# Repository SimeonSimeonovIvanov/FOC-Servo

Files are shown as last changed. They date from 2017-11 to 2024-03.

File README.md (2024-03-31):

# FOC-Servo

[FOC Servo (youtube.com)](https://www.youtube.com/playlist?list=PLE616v1yP137koahQjisksADdZlHxYS2S)<br>
[Images (photos.google.com)](https://goo.gl/photos/JQcb6tujQgFE7cGe8)<br>

![Screen Shot](https://lh3.googleusercontent.com/vWZbaQVdAhu1QQO_cTlWY4MgnAb2BmGCg2ht9W3ZADUsB-J3ieZKUOjoW8N4zHFRGdZp8hFGPKCy6uawGKFupMPxBJmIFaj5hGluz3LkEmy5S17hmuiLZEQlVxxbsq9VOWg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)<br>
![Screen Shot](https://lh3.googleusercontent.com/k02gDKrigeXRs4gnt29zIekYWgJM7NDDvpPBwwBkn84v4wwCzqt8nw-INf11CDgn7xQ7Py5mxIiK_7V0SbNQoPlOT3bTszP4-zwKSuMI01aGK7_4IhnsZZ5Z7r1dPS8m6I9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)<br>

http://mcu-bg.com/mcu_site/viewtopic.php?p=226271#p226271:<br>
"След аналоговото DC-Servo (viewtopic.php?f=22&t=13129) започнах работа по BLDC-Servo. Работих по хардуерен синусоидален контрол на AC Servo motor (PMSM) с три токови ШИМ-а. Успях да постигна токова регулация в 6 стъпкова комутация. Синусоидален режим така и не подкарах напълно. Но в крайна сметка това беше само за упражнение. Целта през цялото време беше векторно управление (FOC) на мотора. Самия мотор претърпя малка реконструкция - изведох сигналите за комутация UVW навън през RS422 предавател.

В крайна сметка стигнах до FOC-Servo. За момента имам реализирано векторно управление на базата на STM32F4. Липсва обратна връзка по скорост. Директно задавам позиция от импулсен генератор. Работи добре, има още какво да се желае.

Редно е да отбележа, че токовата обратна връзка минава през модули от честотни задвижвания на Electroinvent. Също и импулсното захранване на електрониката е от компоненти / схема (свалена от платка) на тяхно задвижване. Първоначално силовия мост беше с импулсни DC/DC преобразуватели но в случай на пробив на транзистор си 'заминаваха' набързо. Също SVPWM е копиран от кодa на STM FOC SDK v1. Другите компоненти (софтуер/хардуер) са смесица от мои и чужди проекти.

Продължавам работа по задвижването, изкушавам се да бъде част от бъдещо обновяване на ROBKO-01."

http://mcu-bg.com/mcu_site/viewtopic.php?p=235621#p235621:<br>
"Вече задвижването се захранвана директно от мрежата ( 220 VAC -> 320 VDC на моста ). Изпитвах доста притеснения в етапа на увеличаване на напрежението. Разбира се имаше и проблеми. Сред които особено неприятна осцилация на GS на полевите транзистори. Успях да затворя и позиционния и скоростния контур. За жалост обратната връзка по скорост все още е прекалено груба и това създава проблеми но все пак работи доста добре.

Файловете на проекта са качени в https://github.com/SimeonSimeonovIvanov/FOC-Servo
Видео от отделните тестове: youtube.com / FOC Servo"

http://mcu-bg.com/mcu_site/viewtopic.php?p=277382#p277382:<br>
"Да се похваля :) От проекта за FOC Servo (open source) успях да достигна до нещо много по-истинско: AC Servo. Засега не съм решил дали ще премине към open или close. Отделни схемни решения от него са качени в git: https://github.com/SimeonSimeonovIvanov/"

# AC-Servo
[AC Servo ( MCU v.0.0.1 / IPM v.0.0.2 ) (photos.google.com)](https://photos.app.goo.gl/KCEzDaz5cRpWHHwj6)<br>
[AC Servo (photos.google.com)](https://photos.app.goo.gl/785x7djrvYAcP9JZ6)<br>
[AC Servo ( Work ) (photos.google.com)](https://photos.app.goo.gl/srzg5DDZzGg4B8dc7)<br>

![Screen Shot](https://lh3.googleusercontent.com/InO0-X00L5HjlXPxuh1YEjHJFSkUZFtOApBEi4UaxSTPb9P_QFyURlaM9I8N8cGii7pULpo6o4EXxeGouaYiY4lC6Kz6RivBfqiPAh9K2oRpcYkvYIHu17OkECJ6e2FBvHD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)<br>

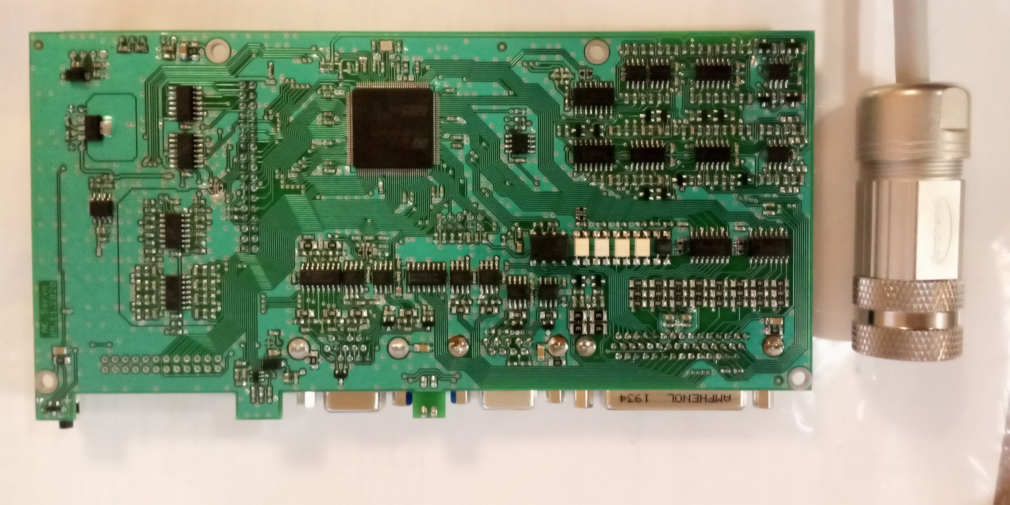
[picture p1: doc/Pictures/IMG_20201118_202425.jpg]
<br>
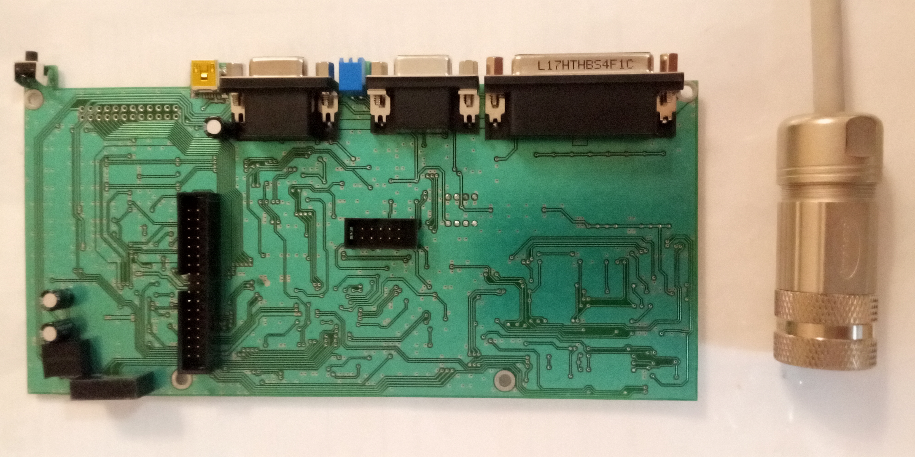
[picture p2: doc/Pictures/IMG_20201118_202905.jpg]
<br>

MIGE 80ST-M02430<br>
https://youtu.be/u-dZzM7kjZM: 300 to 3000 rpm<br><br>
SANYO DENKI P50B04006DXS40E<br>
https://youtu.be/c_Dg6a0bA2k: IN: 230 VAC; DC Bus: 325 VDC<br>
https://youtu.be/9ND_6Mmglnc<br>
![Screen Shot](https://lh3.googleusercontent.com/okfIJzOqILg2Vj1FPi2K5oUJk9owYkxtr5FeaoL3CWSu0oE8lGGliDmks5RnoqhALW29WYXMFR0nzFvj4oWKjR9dDEuZ9FIdgU9OOmerqA_8B_PouIPbHv3mtwUzUjZpZbU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)<br>

AM3024-0C21-0000<br>
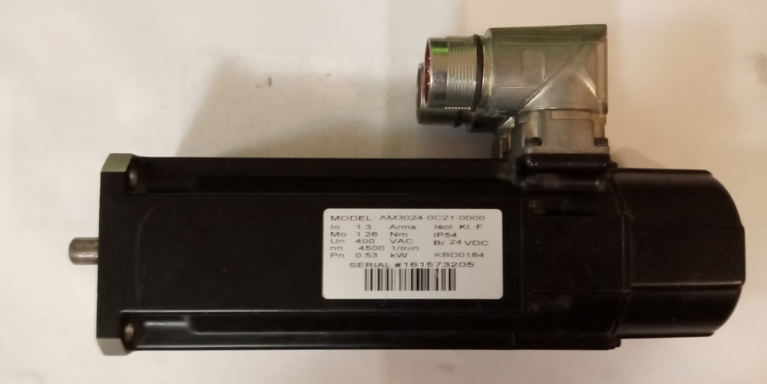
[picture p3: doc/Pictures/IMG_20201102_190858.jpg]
<br>

XML-SE30AЕКЕ<br>
https://youtu.be/lwz9wlfNBrg?si=XCSkZ5ty04_A1IbP<br>
https://youtube.com/shorts/MPl2bm2EVfs: AC Servo and Grlb - before bearing replace<br>
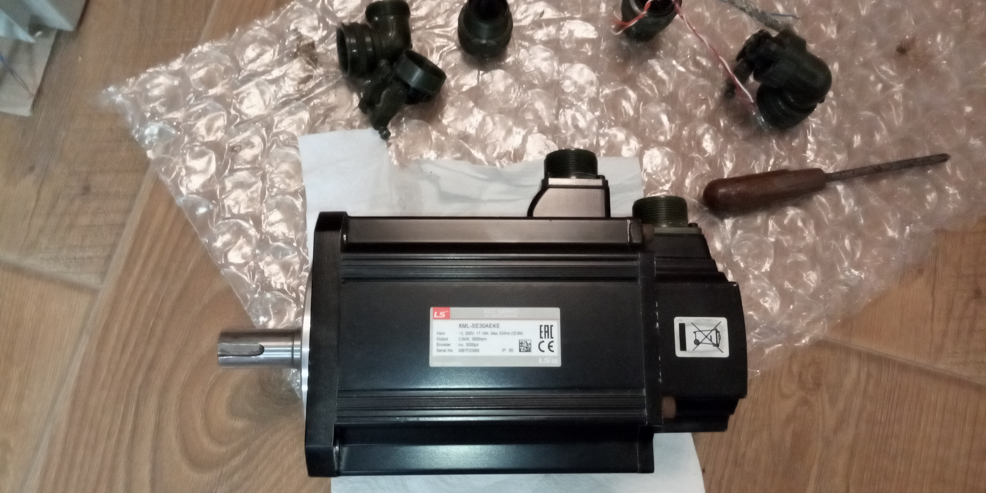
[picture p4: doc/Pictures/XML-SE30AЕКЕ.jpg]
<br>

APM-SC08ADK-52<br>
https://youtu.be/YavCcIHJMfQ?si=W7gMHxK1SwErK5KL<br>

# Simulation:

FOC.grf.png:
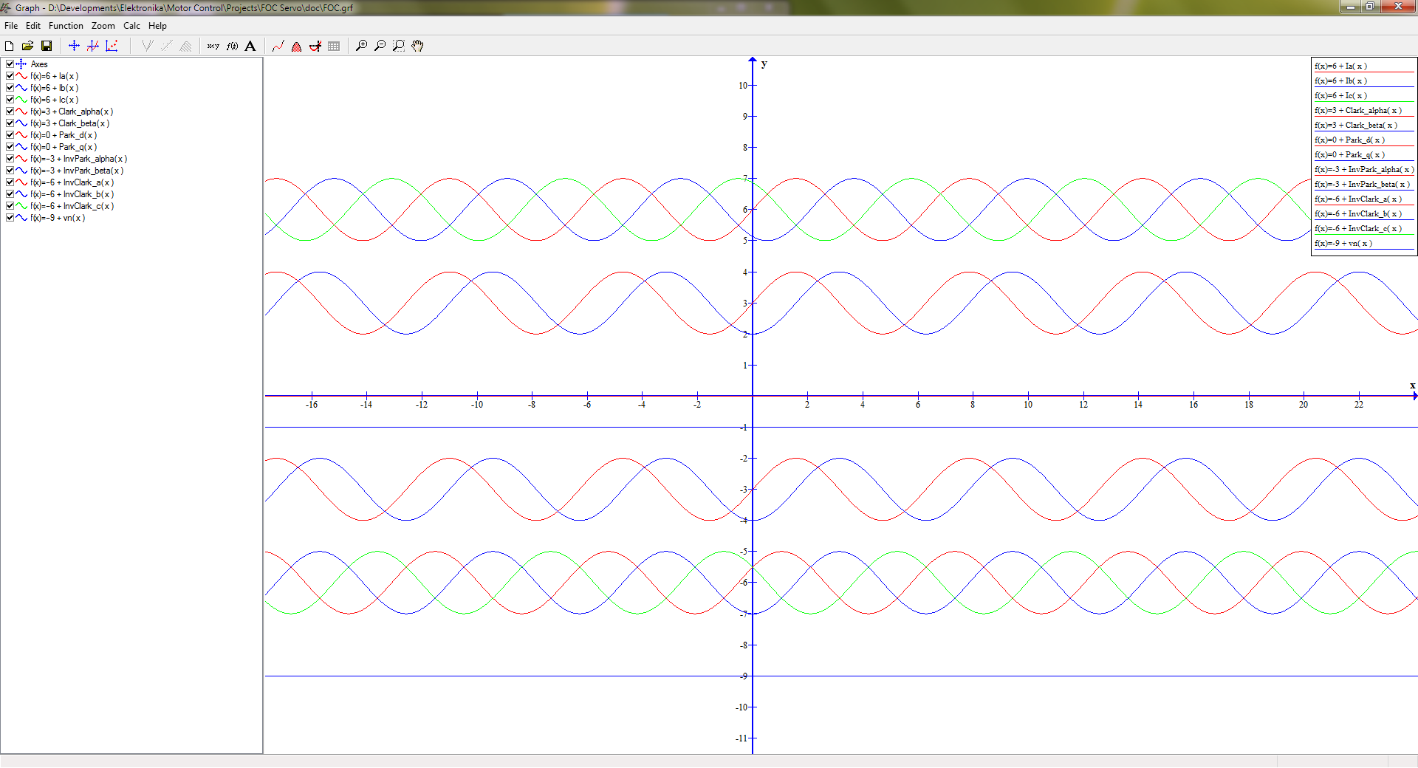
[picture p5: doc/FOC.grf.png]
<br>

ATAN.grf.png
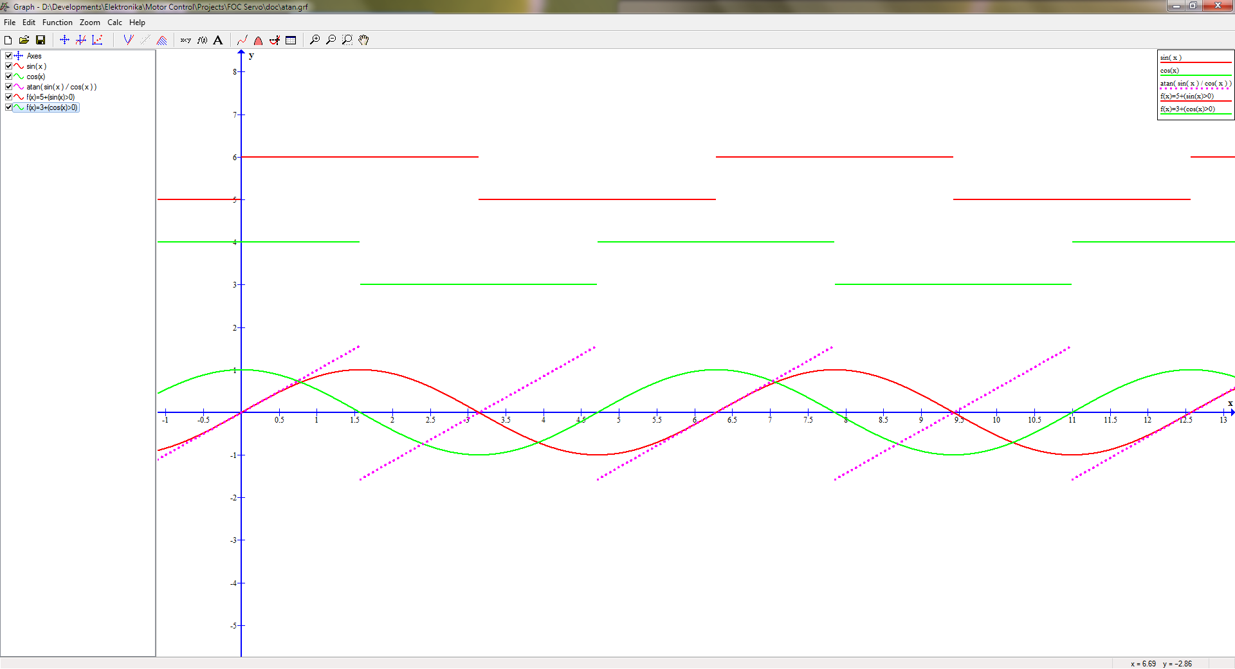
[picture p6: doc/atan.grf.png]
<br>

Sin/Cos Encoder:
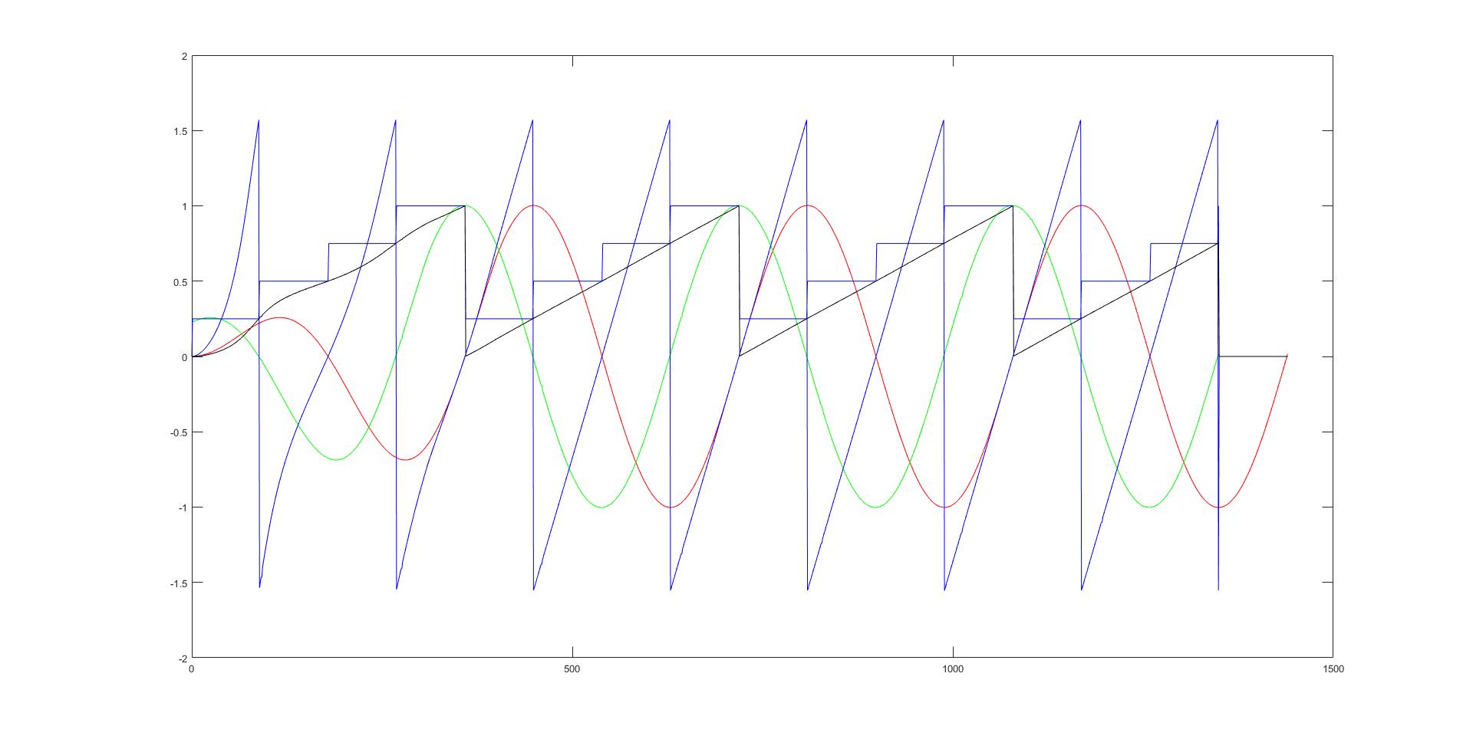
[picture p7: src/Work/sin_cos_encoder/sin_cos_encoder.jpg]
<br>

Bipolar Analog Output:
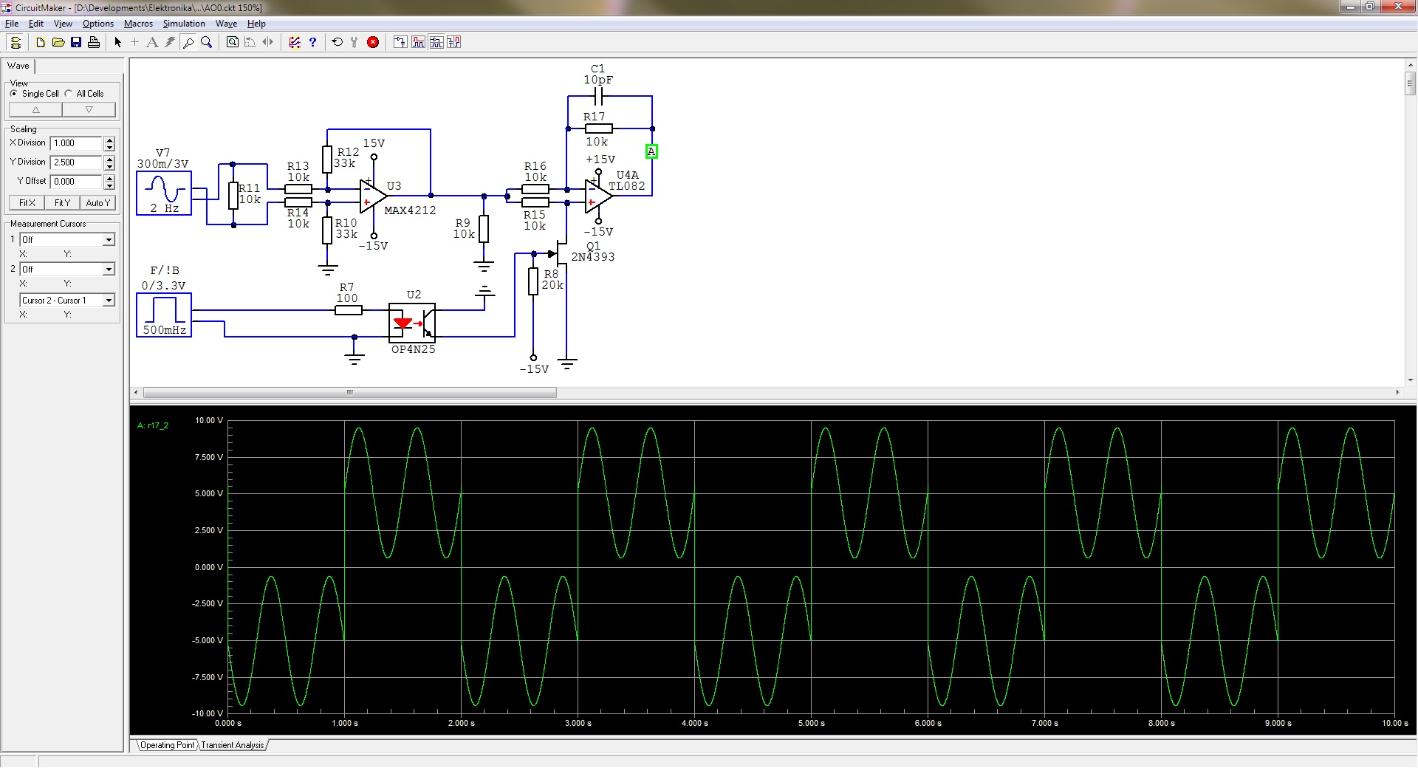
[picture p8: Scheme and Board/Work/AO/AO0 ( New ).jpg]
<br>

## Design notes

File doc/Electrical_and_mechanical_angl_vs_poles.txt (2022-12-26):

https://www.researchgate.net/post/Is_there_a_relation_between_the_electrical_and_mechanical_angle
========================================================================================================================
Nebi Caka
University of Prishtina
In a multipolar electrical machine (motor or generator), relationship between the mechanical angle and electrical angle is given by:
Electrical angle = (P/2) x Mechanical angle
where: P = Number of poles
So:
- In a two-pole motor (P = 2): Electrical Angle = Mechanical Angle
- In a four-pole motor (P = 4): Electrical Angle = 2 times Mechanical Angle
- In a six-pole motor (P = 6): Electrical Angle = 3 times Mechanical Angle
etc.
========================================================================================================================
Aderiano da Silva
Rockwell Automation
For asynchronous machines, the electrical angle (thetaE) is related to the mechanical angle (thetaM) in terms of the number of poles (N) as follows:
thetaE = (N/2) * thetaM
========================================================================================================================

Pole pairs = Poles / 2

Electrical angle = (Poles / 2) x Mechanical angle
Electrical angle = Pole pairs x Mechanical angle

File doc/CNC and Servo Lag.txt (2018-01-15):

http://www.practicalmachinist.com/vb/cnc-machining/lag-error-234762/#post1679838

 mike_kilroy
mike_kilroy is offline Stainless 

system gain (amount of "lag" error) is SET by the analog velocity speed scale adjustment pot on the servo drive amplifier. it was typically set to 1IPM/MiL on that vintage machine. that means if u run 100IPM u will have .100" or 100 mills of following ("lag") error. 400ipm means .4" so u can see the faster u go the more lag.

then there is a max lag error shut off point - maybe 1" or so in the above ex for a machine that can run to 400ipm.

yes, if it used to work somethng likely changed so mechanics is first thing to look at; if friction increases then the lag might increase (depends on the servo drive design - if it has integral gain - the I in PID loop then it takes a LOT of extra friction to bother this).

if you can turn the screw by hand easy and dont think it changed it could be aging of electronics and a simple readjust of speed pot on Y axis servo drive will bring it back.

remember that WHEN something brakes it is usually the last thing we did that caused it to brake.... so think back..... did this y shake and error start suddendly? after a crash? or did it creep up on you getting worse and worse -- over 1 day? 1 hour? 2 years? these r all good clues to help point to the culprit

if u can see lag error and speed on ur nc screen, check all axis; they shyud be the same. if u see y has bigger lag at a given speed, adjust the speed pot on the drive to make it the sanme as the other axes. if u dont know where the speed pot is, tell us the drive mfgr and model cuz some of us may know

too hi or too lo gain will cause the same y axis oscillation or jerkyness you see.

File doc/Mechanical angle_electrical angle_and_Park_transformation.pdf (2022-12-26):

Electrical Engineering Stack Exchange is a question and answer site for electronics and electrical engineering professionals, students, and enthusiasts. It only takes a minute to sign
up.

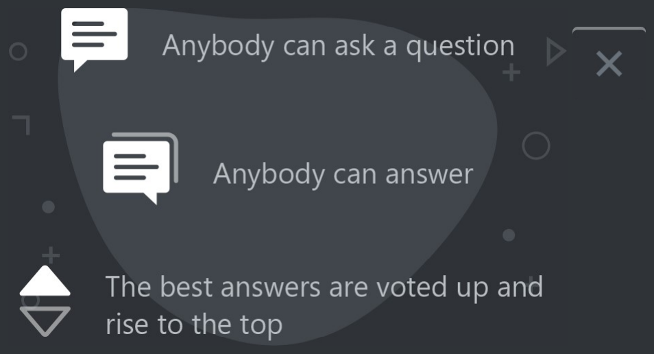
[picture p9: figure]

# Mechanical angle, electrical angle, and Park transformation

Asked 5 years, 7 months ago Modified 5 years, 2 months ago 2k times Viewed
0

I have a question about the electrical angle and mechanical angle of the BLDC motor. The motor has 8 poles. We have
Electrical angle = number of pole pair * mechanical angle
This would mean that if the mechanical angle covers 45 deg, the electrical angle has spanned 360 deg. After that, should I reset my electrical angle to 0 and start counting again, or it's acceptable if the electrical angle keeps increasing?
I use the electrical angle in the Park transformation for calculations.
microcontroller motor
Share Cite Follow | edited Oct 25, 2017 at 10:03
raggot
415 4 16

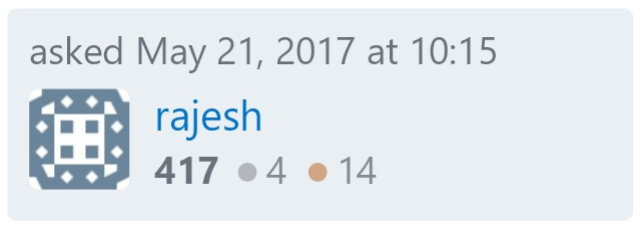
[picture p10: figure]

1 Robert Park was a man- please capitalize his name in your title and text. – Spehro Pefhany May 21, 2017 at 10:37
I am sorry. Can i edit now. – | May 21, 2017 at 10:49
1 Answer | Sorted by: Highest score (default)

1

What is key is the electrical frame of reference. Every pole-pair the cycle completes.
For a 6 pole machine, 3pole-pair, this wrap (in the mechanical frame of reference) is every 120degrees
For an 8 pole machine, 4pole-pair, this wrap (in the mechanical frame of reference) is every 90degrees.
If you unwrap a machine stator (see below for a 2pole-pair) the difference becomes clear

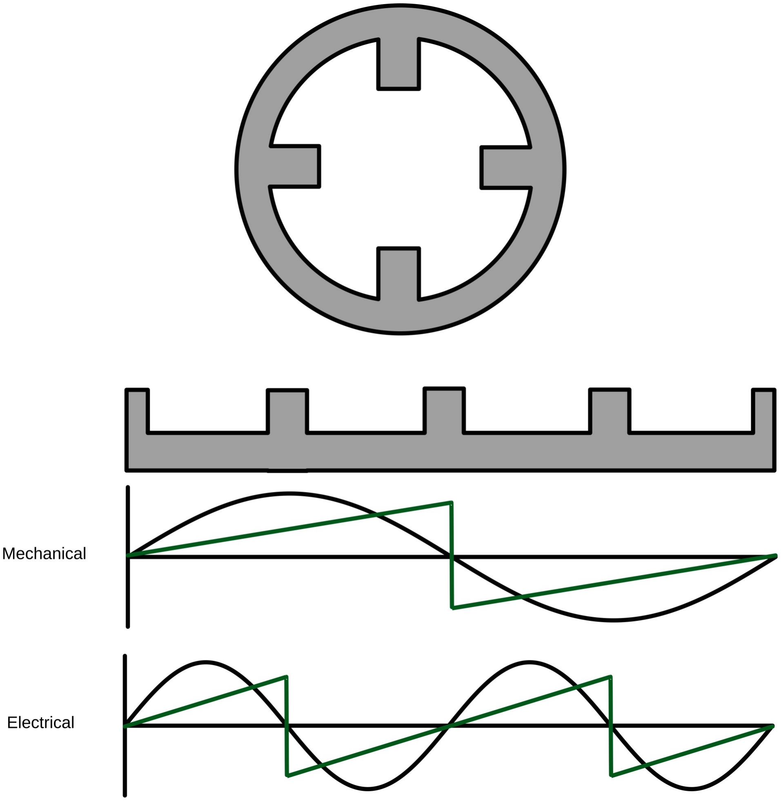
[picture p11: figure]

Share Cite Follow | answered May 21, 2017 at 10:58
user16222

No i am not able to understand. – May 21, 2017 at 11:06
What exactly don't you understand – user16222 May 21, 2017 at 11:11
If my mechanical angle is 360 then electrical angle will be 8 * 360 degrees, if it is 8 pole pair. Please help. – May 21, 2017 at 11:12
The electrical angle would be 0 or 4*360 (as 0=360) if you were to unwrap the angle. I do not know you low level implementation but the usual method is to calculate mechanical, multiply by pole-pair count & ensure the register wraps – user16222 May 21, 2017 at 11:15
void encoderInterrupt(void) { encoderincr++; mechanical_angle = encoderincr * 360 / ENCODER_COUNTER; /* ENCODER_COUNTER is the number of counts for one revolution */ if(mechanical_angle > 360) { encoderincr=0; } electricalangle = NOPOLEPAIR * mechanical_angle; } – May 21, 2017 at 11:51

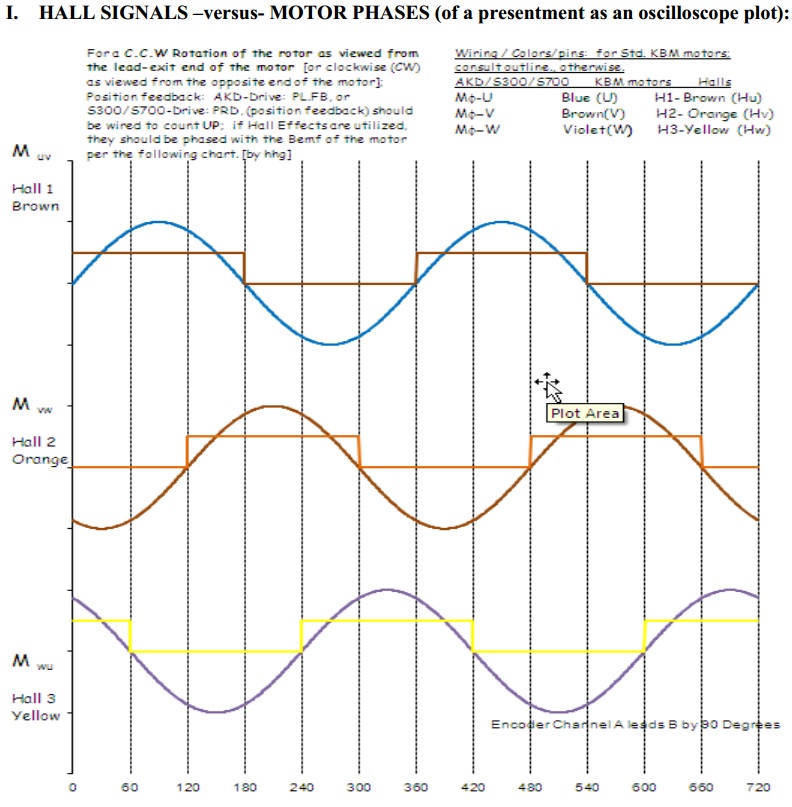
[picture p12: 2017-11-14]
doc/HALL/HALL vs PHASE.jpg

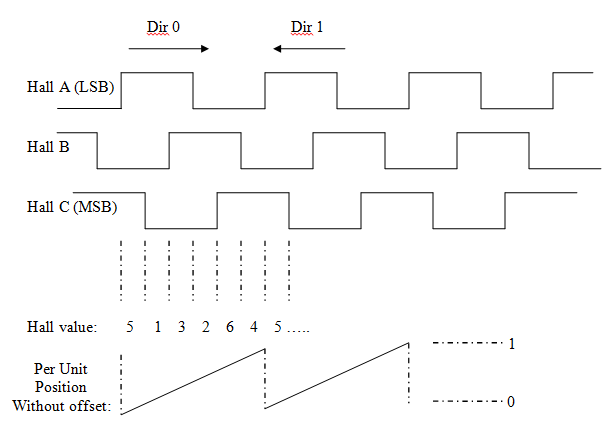
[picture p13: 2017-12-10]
doc/HALL/xxc2812pmsmfoc_Hall_signals.png

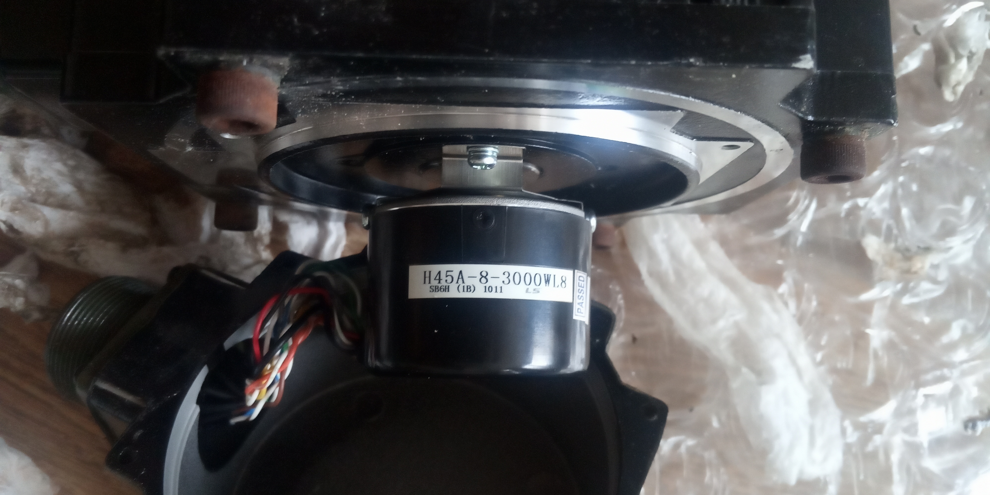
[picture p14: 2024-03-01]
doc/Pictures/H45A-8-3000WL8.jpg

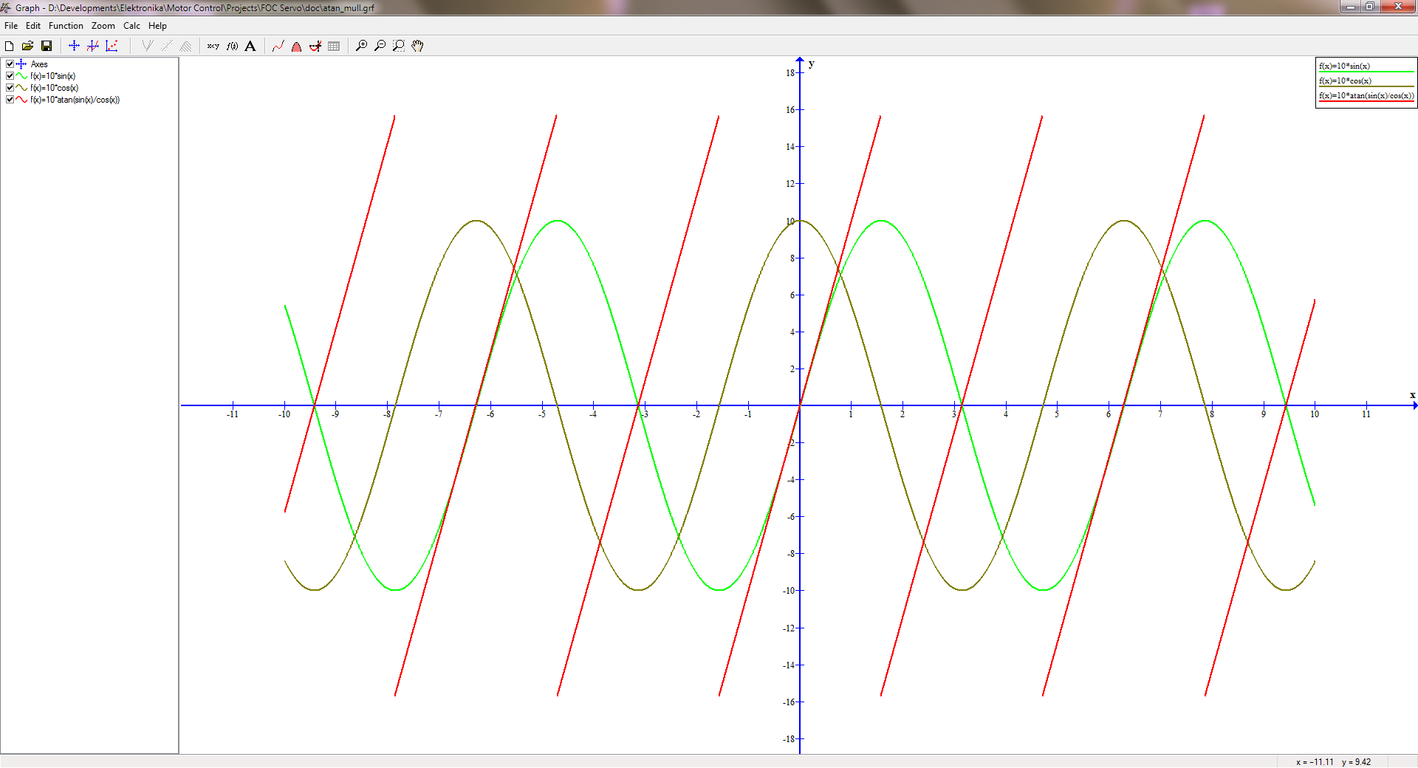
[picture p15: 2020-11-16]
doc/atan_mull.grf.png

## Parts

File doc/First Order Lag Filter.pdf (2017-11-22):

# First Order Lag Filter

The formula for a first order lag filter is fairly simple:

new_filtered_value = k * raw_sensor_value + (1 - k) * old_filtered_value

The "magic" is determining an approprate value for 'k'. The hard approach is to characterize the noise which will be present in the system and do some frequency-domain calculations to diminish the noise to acceptable levels. One thing that makes this approach hard (or even impossible) is that it requires knowing what noise sources will be present and what their frequency and magnitude characteristics will be. The easier approach is to cast a wide net and just filter the hell out of the signal.

The one catch with the easy approach is known as "lag". That is, when the input changes, the filtered value may not reflect enough of the change fast enough to meet system response requirements. For example, if you are using an IR LED and IR sensor to detect when you are within a short distance of an obstacle, too much filtering may result in the sensor not indicating there is an obstacle until after you run into the obstacle (or after there is insufficient time to stop).

The good thing about working from the perspective of lag is that determining how much lag is acceptable is generally easier than characterizing noise. Consider the previous example about running into an obstacle. If you know that you read the sensor 50 times a second, that you need the filtered value to reach 90% of the actual sensor value before your robot will think there is an obstacle, and that (based on your robot's speed and the sensor range) you need the filtered value to reach that level within 0.3 seconds, then you have all of the data you need to calculate 'k'.

The following sections will:

Explain the input data you need to provide.
Show how to calculate a suitable value for 'k' based on your input.

## Input #1: Maximum Response Time (Tr)

This is the (maximum) amount of time (in seconds) between the instant the raw sensor value changes and the instant the filtered sensor value reflects that change.

For example, say your robot has an IR sensor that detects obstacles within 1 meter and your robot requires 0.2 meters to come to a complete stop. That means your robot can continue traveling full speed at most 1 - 0.2 = 0.8 meters after the sensor detects an obstacle.

Furthermore, say your robot's full speed is 2 meters/second. That means your robot needs to start stopping at most 0.8 / 2 = 0.4 seconds after the sensor detects an obstacle.

Finally, you decide you don't want to set things up so your robot just barely manages to stop in time (with its nose right against the obstacle). Instead, you would like to leave some margin for error. So rather than using 0.4 seconds, you go with a
maximum response time (Tr) of 0.3 seconds (leaving you a 0.1 second margin of error).

## Input #2: Sampling Period (Ts)

This is the amount of time (in seconds) between one reading of the raw sensor value and the next.

For example, if the robot samples the sensor 50 times a second, then the sampling period (Ts) is 1 / 50 = 0.02 seconds. (This is assuming that the sensor is read at roughly regular intervals.)

Note: Your sampling period should generally be at least 4 times (and preferably 10 times or more) smaller than your maximum response time.

## Input #3: Desired Fraction of Change (Frac)

This is the (minimum) accuracy with which a change in the raw sensor value (at time t) will be reflected in the filtered sensor value (at or before time t + Tr).

For example, suppose the output from your IR sensor changes from 0 volts to 2 volts when an obstacle comes into range. Furthermore, your robot considers any value > 1.8 volts to indicate there is an obstacle present. That means that your robot needs to see 1.8 / 2 = 0.9 (90%) of the change before the change will be acted upon, so Frac is 0.9 in this case.

## Calculate k

To calculate k, enter Tr, Ts and Frac from above into the following equation:

k = 1 - eln(1 - Frac) * Ts / Tr

where:

"e" is approximately 2.71828182846, and
"ln" is the natural logorithm function.

For the example values given in the previous sections (Tr = 0.3, Ts = 0.02, Frac = 0.9), k comes out to be about 0.142304101409.

## Results

So, does it actually work as advertised? To demonstrate it in action, the following C code is used:

void test() {
const double Ts = 0.02;
const double k = 0.142304101409; const double old_raw_sensor_value = 0;
const double raw_sensor_value = 2;
double t = 0;
double filtered_value = old_raw_sensor_value; // assume we have settled on the old value do {
filtered_value = k * raw_sensor_value + (1 - k) * filtered_value;
t += Ts;
printf("t = %.02f: filtered value = %.8f\n", t, filtered_value); } while (t < 0.4);
}

And the output produced is:

t = 0.02: filtered value = 0.28460820 t = 0.04: filtered value = 0.52871549 t = 0.06: filtered value = 0.73808531 t = 0.08: filtered value = 0.91766095 t = 0.10: filtered value = 1.07168223 t = 0.12: filtered value = 1.20378566 t = 0.14: filtered value = 1.31709023 t = 0.16: filtered value = 1.41427109 t = 0.18: filtered value = 1.49762271 t = 0.20: filtered value = 1.56911306 t = 0.22: filtered value = 1.63043004 t = 0.24: filtered value = 1.68302136 t = 0.26: filtered value = 1.72812872 t = 0.28: filtered value = 1.76681712 t = 0.30: filtered value = 1.80000000 t = 0.32: filtered value = 1.82846082 t = 0.34: filtered value = 1.85287155 t = 0.36: filtered value = 1.87380853 t = 0.38: filtered value = 1.89176609
t = 0.40: filtered value = 1.90716822

As you can see, the desired filter value (1.8) was achieved in the desired response time (0.3 seconds).

## Beyond k

Handling Startup

What do you do at the start of time? The lag filter formula is undefined because you don't have an "old_filtered_value" yet. Some approaches for computing the very first filtered value are:

Use the raw sensor data instead of the lag filter formula.
Use some "safe" value.
Use the raw sensor data adjusted towards some "safe" value. (Adjust it enough so that the adjustment is likely to be larger than any noise.)

Another option which can be combined with the above is to simply ignore the filtered sensor data entirely until several samples have been run through the filter. (For example, ignore the sensor for 'Tr' time after startup.)

Scaled Integer Math

k is always some value between 0 and 1, and rounding to 0 or 1 is no good, so a straight-forward implementation involves the use of floating point or fixed point. If you are operating in an environment where neither floating point nor fixed point are available/desirable, and you have adequately large integers at your disposal, scaled integer math can be used instead.

Scaled integer math is basically the same as fixed point, except the location of the binary point is implicit in your code. The following is some example code that only uses integer operations (add, subtract, multiply, shift) to implement a lag filter:

// shift_amount is the number of bits past the binary point.
// k_scaled is k times 2 to the power of shift_amount, rounded to the next largest integer.
// The expression "((1 << shift_amount) - k_scaled)" can, of course, be precomputed.

scaled_filtered_value = k_scaled * raw_sensor_value + ((((1 << shift_amount) - k_scaled) * scaled_filtered_value) >> shift_amount)

filtered_value = scaled_filtered_value >> shift_amount

Note that the second product will require the largest number of integer bits. You can reduce the amount of bits required by feeding "filtered_value" instead of "scaled_filtered_value" into the equation (and then removing the ">> shift_amount" in that same equation), but that negatively impacts the accuracy and can result in the 'filtered_value' getting stuck before reaching its target value.

Last Modified: November 11th, 2006
home: http://my.execpc.com/~steidl/e-mail: steidl@execpc.com

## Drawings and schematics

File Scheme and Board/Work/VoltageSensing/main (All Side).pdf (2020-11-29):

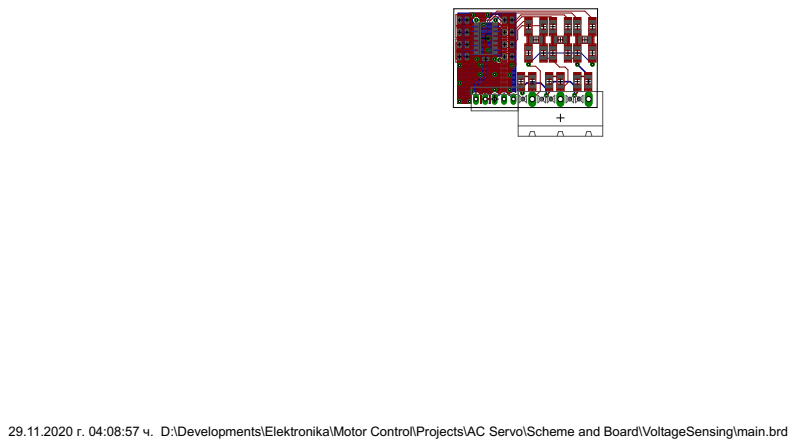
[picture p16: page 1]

29.11.2020 г. 04:08:57 ч. D:\Developments\Elektronika\Motor Control\Projects\AC Servo\Scheme and Board\VoltageSensing\main.brd

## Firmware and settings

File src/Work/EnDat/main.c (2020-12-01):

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
/* Includes ------------------------------------------------------------------*/
#include "main.h"

/* USER CODE BEGIN Includes */
#include <math.h>
#include "endat.h"
#include "foc.h"
/* USER CODE END Includes */

ADC_HandleTypeDef hadc1;
ADC_HandleTypeDef hadc2;
ADC_HandleTypeDef hadc3;
DMA_HandleTypeDef hdma_adc3;

CAN_HandleTypeDef hcan1;

DAC_HandleTypeDef hdac;

SPI_HandleTypeDef hspi3;

TIM_HandleTypeDef htim1;
TIM_HandleTypeDef htim2;
TIM_HandleTypeDef htim3;
TIM_HandleTypeDef htim5;

PCD_HandleTypeDef hpcd_USB_OTG_FS;

/* USER CODE BEGIN PV */
volatile uint8_t encoder_pwr_en = 1;
volatile uint16_t arrADC[15];
volatile float s, c;

volatile int16_t arrADC1[15];
volatile uint16_t arrOffset[15];
volatile uint32_t arrOffsetSum[15];

volatile float angle, delta = 0.0f;
volatile float min = 0, max = 0, angle;

volatile uint16_t tim3;
volatile uint32_t tim5, upos;
volatile int32_t pos;

endat_data_t st_EnDat;

uint8_t main_state = 0;

uint8_t adc_is_ready = 0;
uint32_t sin_sum, cos_sum, average_cnt;

MC_FOC stFoc;
/* USER CODE END PV */

void SystemClock_Config(void);
static void MX_GPIO_Init(void);
static void MX_DMA_Init(void);
static void MX_TIM1_Init(void);
static void MX_TIM2_Init(void);
static void MX_TIM3_Init(void);
static void MX_TIM5_Init(void);
static void MX_ADC1_Init(void);
static void MX_ADC2_Init(void);
static void MX_ADC3_Init(void);
static void MX_DAC_Init(void);
static void MX_SPI3_Init(void);
static void MX_CAN1_Init(void);
static void MX_USB_OTG_FS_PCD_Init(void);
/**
  * @brief  The application entry point.
  * @retval int
  */
int main(void)
{
  /* MCU Configuration--------------------------------------------------------*/

  /* Reset of all peripherals, Initializes the Flash interface and the Systick. */
  HAL_Init();

  /* Configure the system clock */
  SystemClock_Config();

  /* USER CODE BEGIN SysInit */
  focInit( &stFoc );
  createSinCosTable();
  /* USER CODE END SysInit */

  /* Initialize all configured peripherals */
  MX_GPIO_Init();
  MX_DMA_Init();
  MX_TIM1_Init();
  MX_TIM2_Init();
  MX_TIM3_Init();
  MX_TIM5_Init();
  MX_ADC1_Init();
  MX_ADC2_Init();
  MX_ADC3_Init();
  MX_DAC_Init();
  MX_SPI3_Init();
  MX_CAN1_Init();
  MX_USB_OTG_FS_PCD_Init();
  /* USER CODE BEGIN 2 */
  HAL_TIM_PWM_Start( &htim1, TIM_CHANNEL_1 );
  HAL_TIM_PWM_Start( &htim1, TIM_CHANNEL_2 );
  HAL_TIM_PWM_Start( &htim1, TIM_CHANNEL_3 );
  HAL_TIM_PWM_Start( &htim1, TIM_CHANNEL_4 );
  /* USER CODE END 2 */

  /* Infinite loop */
  /* USER CODE BEGIN WHILE */
//en_dat_inti();
  HAL_GPIO_WritePin( GPIOD, ENDAT_CLK_EN_OR_WN_ENABLE_Pin, GPIO_PIN_SET );
  while (1)
  {
	  switch( main_state )
	  {
	  case 0:
		  stFoc.enable = 0;

		  encoder_pwr_en = 0;;
		  sin_sum = 0;
		  cos_sum = 0;
		  average_cnt = 0;
		  main_state = 1;
		  break;

	  case 1:
		  if( average_cnt < 1000 )
		  {
			  average_cnt++;
		  } else {
			  average_cnt = 0;
			  main_state = 2;
		  }
		  break;

	  case 2:
		  if( average_cnt < 8 )
		  {
			  if( adc_is_ready )
			  {
				  average_cnt++;

				  for( int i = 0; i < 15; i++ )
				  {
					  arrOffsetSum[i] += arrADC[i];
				  }

				  adc_is_ready = 0;
			  }
		  } else {
			  for( int i = 0; i < 15; i++ )
			  {
				  arrOffset[i] = arrOffsetSum[i] / 8;
			  }

			  stFoc.current_a_offset = arrOffset[0];
			  stFoc.current_b_offset = arrOffset[4];
			  stFoc.current_c_offset = arrOffset[8];
			  main_state = 3;
		  }
		  break;

	  case 3:
		  encoder_pwr_en = 1;
		  main_state = 4;
		  break;

	  case 4:
		  stFoc.enable = 1;

		  for( int i = 0; i < 15; i++ )
		  {
			  arrADC1[i] = arrADC[i] - arrOffset[i];
		  }

		  if( arrADC1[10] )
		  {
			  int32_t temp;
			  float at;

			  s = arrADC1[6];
			  c = arrADC1[10];
			  at = 4095.0f - ( 4095.0f * (( 1.57079633f + atan( s / c ) ) / 3.14159265f) );

			  //temp = ( ( tim5 % 1023 ) << 12) + ( (uint16_t)at & 0x0fff );
			  temp = ( tim3<<12) + ( (uint16_t)at & 0x0fff );
			  angle= (float)temp / 4096.0f;
			  pos = temp;
		  }

		  //GPIOD->BSRR |= LED2_Pin;
		  endat_func( 0.0f, &st_EnDat );
		  //GPIOD->BSRR |= LED2_Pin<<16;
		  break;
	  }

	  if( encoder_pwr_en )
	  {
		  HAL_GPIO_WritePin(ENCODER_VCC_EN_GPIO_Port, ENCODER_VCC_EN_Pin, GPIO_PIN_RESET);
	  } else {
		  HAL_GPIO_WritePin(ENCODER_VCC_EN_GPIO_Port, ENCODER_VCC_EN_Pin, GPIO_PIN_SET);
	  }

	  HAL_DAC_SetValue( &hdac, DAC_CHANNEL_1, DAC_ALIGN_12B_R, angle+1500 );
	  HAL_DAC_SetValue( &hdac, DAC_CHANNEL_2, DAC_ALIGN_12B_R, 0 );

    /* USER CODE END WHILE */

    /* USER CODE BEGIN 3 */
	  /*uint8_t txEnData[10];

	  txEnData[0] = 0xAA;
	  txEnData[1] = 0x55;

	  HAL_GPIO_WritePin( GPIOD, ENDAT_TX_EN_OR_USART2_RTS_Pin, GPIO_PIN_SET );
	  HAL_SPI_Transmit( &hspi3, txEnData, 10, 1 );
	  HAL_GPIO_WritePin( GPIOD, ENDAT_TX_EN_OR_USART2_RTS_Pin, GPIO_PIN_RESET );*/
  }
  /* USER CODE END 3 */
}

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
/* USER CODE BEGIN 4 */
void ADC_IRQHandler(void)
{
	/*HAL_ADC_IRQHandler(&hadc1);
	HAL_ADC_IRQHandler(&hadc2);
	HAL_ADC_IRQHandler(&hadc3);
	return;*/

	uint32_t tmp1 = 0U;//, tmp2 = 0U;

	GPIOC->BSRR |= LED1_Pin;

	tim3 = TIM3->CNT;
	tim5 = TIM5->CNT;

	tmp1 = __HAL_ADC_GET_FLAG( &hadc1, ADC_FLAG_EOC );
	//tmp2 = __HAL_ADC_GET_IT_SOURCE( &hadc1, ADC_IT_EOC );
	if( tmp1 )//&& tmp2 )
	{
		__HAL_ADC_CLEAR_FLAG( &hadc1, ADC_FLAG_STRT | ADC_FLAG_EOC );
	}

	tmp1 = __HAL_ADC_GET_FLAG( &hadc1, ADC_FLAG_JEOC );
	//tmp2 = __HAL_ADC_GET_IT_SOURCE( &hadc1, ADC_IT_JEOC );
	if( tmp1 )//&& tmp2 )
	{
		arrADC[0] = ADC1->JDR1;
		arrADC[1] = ADC1->JDR2;
		arrADC[2] = ADC1->JDR3;
		arrADC[3] = ADC1->JDR4;

		__HAL_ADC_CLEAR_FLAG( &hadc1, (ADC_FLAG_JSTRT | ADC_FLAG_JEOC) );
	}

	tmp1 = __HAL_ADC_GET_FLAG( &hadc2, ADC_FLAG_EOC );
	//tmp2 = __HAL_ADC_GET_IT_SOURCE( &hadc2, ADC_IT_EOC );
	if( tmp1 )//&& tmp2 )
	{
		__HAL_ADC_CLEAR_FLAG( &hadc2, ADC_FLAG_STRT | ADC_FLAG_EOC );
	}

	tmp1 = __HAL_ADC_GET_FLAG( &hadc2, ADC_FLAG_JEOC );
	//tmp2 = __HAL_ADC_GET_IT_SOURCE( &hadc2, ADC_IT_JEOC );
	if( tmp1 )//&& tmp2 )
	{
		arrADC[4] = ADC2->JDR1;
		arrADC[5] = ADC2->JDR2;
		arrADC[6] = ADC2->JDR3;
		arrADC[7] = ADC2->JDR4;

		__HAL_ADC_CLEAR_FLAG( &hadc2, (ADC_FLAG_JSTRT | ADC_FLAG_JEOC) );
	}

	tmp1 = __HAL_ADC_GET_FLAG( &hadc3, ADC_FLAG_EOC );
	//tmp2 = __HAL_ADC_GET_IT_SOURCE( &hadc3, ADC_IT_EOC );
	if( tmp1 )//&& tmp2 )
	{
		__HAL_ADC_CLEAR_FLAG( &hadc3, ADC_FLAG_STRT | ADC_FLAG_EOC );
	}

	tmp1 = __HAL_ADC_GET_FLAG( &hadc3, ADC_FLAG_JEOC );
	//tmp2 = __HAL_ADC_GET_IT_SOURCE( &hadc3, ADC_IT_JEOC );
	if( tmp1 ) //&& tmp2 )
	{
		arrADC[8] = ADC3->JDR1;
		arrADC[9] = ADC3->JDR2;
		arrADC[10] = ADC3->JDR3;
		arrADC[11] = ADC3->JDR4;

		__HAL_ADC_CLEAR_FLAG( &hadc3, (ADC_FLAG_JSTRT | ADC_FLAG_JEOC) );
	}

	adc_is_ready = 1;

	stFoc.current_a = arrADC[0];
	stFoc.current_b = arrADC[4];
	stFoc.current_c = arrADC[8];
	adc_current_filter( (uint16_t*)&stFoc.current_a, (uint16_t*)&stFoc.current_b, (uint16_t*)&stFoc.current_c, 2 );

	if( 4 == main_state )
	{
		extern volatile uint64_t post;

		mcFocSetAngle( &stFoc, post % ROTOR_ENCODER_PERIOD );
		mcRunFoc( &stFoc );
	}

	GPIOC->BSRR |= LED1_Pin<<16;
}

void main_callback(void)
{
	static float sum = 0.0f, old = 0.0f;
	static int c = 0;

	if( c < 4 )
	{
		sum += ( angle - old );
		c++;
	} else {
		sum = sum / 4.0f;
		if( fabs(sum) < 0.0001 )
		{
			sum = 0.00011f;
		}
		delta = fabs(sum);
		sum = 0;
		c = 0;
	}

	old = angle;
}

float arr_sin[ ROTOR_ENCODER_PERIOD + 1 ], arr_cos[ ROTOR_ENCODER_PERIOD + 1 ];

void createSinCosTable(void)
{
	for( int i = 0; i <= ROTOR_ENCODER_PERIOD; i++ ) {
		arr_sin[i] = sinf( deg_to_rad( (float)i * ( 360.0f / (float)ROTOR_ENCODER_PERIOD ) ) );
		arr_cos[i] = cosf( deg_to_rad( (float)i * ( 360.0f / (float)ROTOR_ENCODER_PERIOD ) ) );
	}
}

float fSinAngle(int angle)
{
	return arr_sin[angle];
}

float fCosAngle(int angle)
{
	return arr_cos[angle];
}

/* USER CODE END 4 */
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


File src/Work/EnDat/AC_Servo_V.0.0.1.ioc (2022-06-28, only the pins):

Mcu.UserName=STM32F407ZGTx
PA0-WKUP.GPIO_Label=ENC_A_TIM5_CH1
PA0-WKUP.Signal=S_TIM5_CH1
PA1.GPIO_Label=ENC_B_TIM5_CH2
PA1.Signal=S_TIM5_CH2
PA10.GPIO_Label=USB_ID
PA10.Signal=USB_OTG_FS_ID
PA11.GPIO_Label=USB_DM
PA11.Signal=USB_OTG_FS_DM
PA12.GPIO_Label=USB_DP
PA12.Signal=USB_OTG_FS_DP
PA13.GPIO_Label=SWDIO
PA13.Signal=SYS_JTMS-SWDIO
PA14.GPIO_Label=SWCLK
PA14.Signal=SYS_JTCK-SWCLK
PA15.GPIO_Label=HPULSE_TIM2_CH1
PA15.Signal=S_TIM2_CH1_ETR
PA2.GPIO_Label=ADC123_IN2
PA2.Signal=ADCx_IN2
PA3.GPIO_Label=ADC123_IN3
PA3.Signal=ADCx_IN3
PA4.GPIO_Label=DAC1_OUT
PA4.Signal=COMP_DAC1_group
PA5.GPIO_Label=DAC2_OUT
PA5.Signal=COMP_DAC2_group
PA6.GPIO_Label=ROT_POS_TIM3_CH1
PA6.Signal=S_TIM3_CH1
PA7.GPIO_Label=ROT_POS_TIM3_CH2
PA7.Signal=S_TIM3_CH2
PA8.GPIO_Label=USB_PU_RES
PA8.Signal=GPIO_Input
PA9.GPIO_Label=OTG_FS_VBUS
PA9.Signal=USB_OTG_FS_VBUS
PB0.GPIO_Label=ADC12_IN8
PB0.Signal=ADCx_IN8
PB1.GPIO_Label=DC_BUS
PB1.Signal=ADCx_IN9
PB10.GPIO_Label=LDIG4
PB10.Signal=GPIO_Output
PB11.GPIO_Label=LDIG5
PB11.Signal=GPIO_Output
PB12.GPIO_Label=LDIG6
PB12.Signal=GPIO_Output
PB13.GPIO_Label=LDIG7
PB13.Signal=GPIO_Output
PB14.GPIO_Label=LDIG0_SEL0
PB14.Signal=GPIO_Output
PB15.GPIO_Label=LDIG0_SEL1
PB15.Signal=GPIO_Output
PB2.GPIO_Label=BOOT1
PB2.Signal=GPIO_Input
PB3.GPIO_Label=HSIGN_TIM2_CH2
PB3.Signal=S_TIM2_CH2
PB4.GPIO_Label=DI0
PB4.Signal=GPIO_Input
PB5.GPIO_Label=DI1
PB5.Signal=GPIO_Input
PB6.GPIO_Label=DI2
PB6.Signal=GPIO_Input
PB7.GPIO_Label=DI3
PB7.Signal=GPIO_Input
PB8.GPIO_Label=DI4
PB8.Signal=GPIO_Input
PB9.GPIO_Label=DI5
PB9.Signal=GPIO_Input
PC0.GPIO_Label=ENC_SIN
PC0.Signal=ADCx_IN10
PC1.GPIO_Label=ENC_COS
PC1.Signal=ADCx_IN11
PC10.GPIO_Label=ENDAT_SPI3_CLK_OR_USART3_TX
PC10.Signal=SPI3_SCK
PC11.GPIO_Label=ENDAT_SPI3_MISO_OR_USART3_RX
PC11.Signal=SPI3_MISO
PC12.GPIO_Label=ENDAT_SPI3_MOSI_OR_USART3_CK
PC12.Signal=SPI3_MOSI
PC13-ANTI_TAMP.GPIO_Label=AI01_SH
PC13-ANTI_TAMP.Signal=GPIO_Output
PC14-OSC32_IN.GPIO_Label=FAN_EN
PC14-OSC32_IN.Signal=GPIO_Output
PC15-OSC32_OUT.GPIO_Label=FAULT_W
PC15-OSC32_OUT.Signal=GPIO_Input
PC2.GPIO_Label=RES_SIN
PC2.Signal=ADCx_IN12
PC3.GPIO_Label=RES_COS
PC3.Signal=ADCx_IN13
PC4.GPIO_Label=CURRENT_U
PC4.Signal=ADCx_IN14
PC5.GPIO_Label=CURRENT_V
PC5.Signal=ADCx_IN15
PC6.GPIO_Label=PULSE_TIM8_CH1
PC6.Signal=S_TIM8_CH1
PC7.GPIO_Label=SIGN_TIM8_CH2
PC7.Signal=S_TIM8_CH2
PC8.GPIO_Label=LED1
PC8.Signal=GPIO_Output
PC9.GPIO_Label=ENC_Z
PC9.Signal=S_TIM3_CH4
PD0.GPIO_Label=CAN1_RX
PD0.Signal=CAN1_RX
PD1.GPIO_Label=CAN1_TX
PD1.Signal=CAN1_TX
PD10.GPIO_Label=LDIG4_SEL
PD10.Signal=GPIO_Output
PD11.GPIO_Label=LDIG5_SEL
PD11.Signal=GPIO_Output
PD12.GPIO_Label=TIM4_CH1
PD12.Signal=S_TIM4_CH1
PD13.GPIO_Label=ENC_U
PD13.Signal=S_TIM4_CH2
PD14.GPIO_Label=ENC_V
PD14.Signal=S_TIM4_CH3
PD15.GPIO_Label=ENC_W
PD15.Signal=S_TIM4_CH4
PD2.GPIO_Label=ENDAT_CLK_EN_OR_WN_ENABLE
PD2.Signal=GPIO_Output
PD3.GPIO_Label=LED2
PD3.Signal=GPIO_Output
PD4.GPIO_Label=ENDAT_TX_EN_OR_USART2_RTS
PD4.Signal=GPIO_Output
PD5.GPIO_Label=USART2_TX
PD5.Signal=USART2_TX
PD6.GPIO_Label=USART2_RX
PD6.Signal=USART2_RX
PD7.GPIO_Label=OUT0
PD7.Signal=GPIO_Output
PD8.GPIO_Label=LDIG2_SEL
PD8.Signal=GPIO_Output
PD9.GPIO_Label=LDIG3_SEL
PD9.Signal=GPIO_Output
PE0.GPIO_Label=DI6
PE0.Signal=GPIO_Input
PE1.GPIO_Label=DI7
PE1.Signal=GPIO_Input
PE10.GPIO_Label=TIM1_CH2N
PE10.Signal=TIM1_CH2N
PE11.GPIO_Label=TIM1_CH2
PE11.Signal=S_TIM1_CH2
PE12.GPIO_Label=TIM1_CH3N
PE12.Signal=TIM1_CH3N
PE13.GPIO_Label=TIM1_CH3
PE13.Signal=S_TIM1_CH3
PE14.Signal=GPIO_Input
PE15.GPIO_Label=FAULT_PWM_DISABLE_TIM1_BKIN
PE15.Signal=TIM1_BKIN
PE2.GPIO_Label=AI0_SBIT
PE2.Signal=GPIO_Input
PE3.GPIO_Label=AI1_SBIT
PE3.Signal=GPIO_Input
PE4.GPIO_Label=DAC2_SBIT
PE4.Signal=GPIO_Output
PE5.GPIO_Label=DAC1_SBIT
PE5.Signal=GPIO_Output
PE6.GPIO_Label=DAC12_SH
PE6.Signal=GPIO_Output
PE7.GPIO_Label=LDIG3
PE7.Signal=GPIO_Output
PE8.GPIO_Label=TIM1_CH1N
PE8.Signal=TIM1_CH1N
PE9.GPIO_Label=TIM1_CH1
PE9.Signal=S_TIM1_CH1
PF0.GPIO_Label=I2C2_SDA
PF0.Signal=I2C2_SDA
PF1.GPIO_Label=I2C2_SCL
PF1.Signal=I2C2_SCL
PF10.GPIO_Label=FAULT_IPM
PF10.Signal=GPIO_Input
PF11.GPIO_Label=POWER_STAGE_EN
PF11.Signal=GPIO_Output
PF12.GPIO_Label=FAULT_V
PF12.Signal=GPIO_Input
PF13.GPIO_Label=FAULT_U
PF13.Signal=GPIO_Input
PF14.GPIO_Label=FAULT_RST
PF14.Signal=GPIO_Input
PF15.GPIO_Label=LDIG0
PF15.Signal=GPIO_Output
PF2.GPIO_Label=BREAK_RES
PF2.Signal=GPIO_Output
PF3.GPIO_Label=ENCODER_VCC_EN
PF3.Signal=GPIO_Output
PF4.GPIO_Label=ENCODER_OC
PF4.Signal=GPIO_Input
PF5.GPIO_Label=MOTOR_TEMP_ADC3_IN15
PF5.Signal=ADC3_IN15
PF6.GPIO_Label=CURRENT_W
PF6.Signal=ADC3_IN4
PF7.GPIO_Label=AI0_ADC3_IN5
PF7.Signal=ADC3_IN5
PF8.GPIO_Label=AI1_ADC3_IN6
PF8.Signal=ADC3_IN6
PF9.GPIO_Label=IPM_TEMP_ADC3_IN7
PF9.Signal=ADC3_IN7
PG0.GPIO_Label=LDIG1
PG0.Signal=GPIO_Output
PG1.GPIO_Label=LDIG2
PG1.Signal=GPIO_Output
PG10.GPIO_Label=OUT1
PG10.Signal=GPIO_Output
PG11.GPIO_Label=OUT2
PG11.Signal=GPIO_Output
PG12.GPIO_Label=RS485_DE_USART6_RTS
PG12.Signal=USART6_RTS
PG13.GPIO_Label=OUT3
PG13.Signal=GPIO_Output
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

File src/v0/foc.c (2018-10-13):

#include <string.h>
#include "foc.h"

#define __IQ_CONTROL__              0
#define __AI1_SET_SPEED__           1 // +++ ?
#define __POS_AND_SPEED_CONTROL__   2 // +++ ?

#define __CONTROL_MODE__            __AI1_SET_SPEED__//__POS_AND_SPEED_CONTROL__

const float P = 8192.0f;
const float fc = 3*4000000.0f;

const int Ts_rep_counter = 20;
float Ts;

extern uint32_t uwTIM10PulseLength;
extern int16_t tim8_overflow;

float vel;

int32_t sp_pos, pv_pos, sp_counter;
float sp_speed, pv_speed;
int16_t enc_delta;

uint16_t ai0, ai1, ADC_values[ARRAYSIZE];
float ai0_filtered_value;

PID pidPos, pidSpeed;

static int32_t arrSpPos[10];
static volatile LP_MC_FOC lpFoc;

void focInit(LP_MC_FOC lpFocExt)
{
	lpFoc = lpFocExt;

	memset( lpFoc, 0, sizeof( MC_FOC ) );

	lpFoc->fMaxRPM = 3000.0f;

	lpFoc->Ubus = 320;
	lpFoc->Us = 200.0f;

	lpFoc->Usmax = ( 2.0f / 3.0f ) * lpFoc->Ubus;
	lpFoc->m = lpFoc->Us / lpFoc->Usmax;

	lpFoc->Id_des = 0.0f;

	///////////////////////////////////////////////////////////////////////////

	sp_pos = 0;
	pv_pos = 0;
	sp_speed = 0;
	pv_speed = 0;
	sp_counter = 0;

	///////////////////////////////////////////////////////////////////////////
	/*        EATON Wiring Manual | 2011
	 * "The rotation direction of a motor is always
	 * determined by directly looking at the drive
	 * shaft of the motor (from the drive end). On
	 * motors with two shaft ends, the driving end
	 * is denoted with D (= Drive), the non-driving
	 * end with N (= No drive)."
	 */
	lpFoc->fMaxRPMforCW  = 3000.00; // FWD - forward run ( +, clockwise rotation field )
	lpFoc->fMaxRPMforCCW = 3000.00; // REV - reverse run ( -, anticlockwise rotation field active )

	if( lpFoc->fMaxRPMforCW > lpFoc->fMaxRPM ) {
		lpFoc->fMaxRPMforCW = lpFoc->fMaxRPM;
	}

	if( lpFoc->fMaxRPMforCCW > lpFoc->fMaxRPM ) {
		lpFoc->fMaxRPMforCCW = lpFoc->fMaxRPM;
	}
	///////////////////////////////////////////////////////////////////////////

#if ( __CONTROL_MODE__ == __POS_AND_SPEED_CONTROL__ || __CONTROL_MODE__ == __AI1_SET_SPEED__ )
	pidInit( &pidSpeed, 1.1f, 0.0091f, 0.0f, 1.0f );

	pidSetOutLimit( &pidSpeed, 0.999f, -0.999f );
	pidSetIntegralLimit( &pidSpeed, 0.999f );
	pidSetInputRange( &pidSpeed, 200 );
#endif

#if ( __CONTROL_MODE__ == __POS_AND_SPEED_CONTROL__ )
	pidInit_test( &pidPos, 0.5f, 0.001f, 0.0f, 1.0f );

	pidSetIntegralLimit_test( &pidPos, 3000.0f );
	pidSetOutLimit_test( &pidPos, 3000.0f, -3000.0f );
#endif

	///////////////////////////////////////////////////////////////////////////
	pidInit( &lpFoc->pid_d, 0.12f, 0.0012f, 0.0f, 1.00006f );
	pidSetOutLimit( &lpFoc->pid_d, 0.99f, -0.999f );
	pidSetIntegralLimit( &lpFoc->pid_d, 0.25f );
	pidSetInputRange( &lpFoc->pid_d, 2047.0f );

	pidInit( &lpFoc->pid_q, 0.12f, 0.0012f, 0.0f, 1.00006f );
	pidSetOutLimit( &lpFoc->pid_q, 0.999f, -0.999f );
	pidSetIntegralLimit( &lpFoc->pid_q, 0.25f );
	pidSetInputRange( &lpFoc->pid_q, 2047.0f );
	///////////////////////////////////////////////////////////////////////////

	initHall();
	initEncoder();
	svpwmInit();
	initDAC();

	Ts = Ts_rep_counter * ( 1.0f / (float)svpwmGetFrq() );
}

void initDAC(void)
{
	DAC_InitTypeDef DAC_InitStruct;

	// Init DAC 1 & 2:
	GPIO_InitTypeDef GPIO_InitStructure;
	GPIO_StructInit( &GPIO_InitStructure );
	GPIO_InitStructure.GPIO_Pin = GPIO_Pin_5 | GPIO_Pin_4;
	GPIO_InitStructure.GPIO_Mode = GPIO_Mode_OUT;
	GPIO_InitStructure.GPIO_PuPd = GPIO_PuPd_NOPULL;
	GPIO_Init( GPIOA, &GPIO_InitStructure );

	RCC_APB1PeriphClockCmd( RCC_APB1Periph_DAC, ENABLE );

	DAC_StructInit(&DAC_InitStruct );
	DAC_Init( DAC_Channel_1, &DAC_InitStruct );
	DAC_Init( DAC_Channel_2, &DAC_InitStruct );

	DAC_Cmd( DAC_Channel_1, ENABLE );
	DAC_Cmd( DAC_Channel_2, ENABLE );
}

void mcFocSetAngle(LP_MC_FOC lpFoc, int angle)
{
	lpFoc->angle = (float)angle;
	lpFoc->fSinAngle = fSinAngle(angle);
	lpFoc->fCosAngle = fCosAngle(angle);
}

void mcFocCalcCurrent(LP_MC_FOC lpFoc)
{
	lpFoc->Ia = -1.0f * (float)( lpFoc->current_a - lpFoc->current_a_offset );
	lpFoc->Ib = -1.0f * (float)( lpFoc->current_b - lpFoc->current_b_offset );
}

void mcClark(LP_MC_FOC lpFoc)
{
	lpFoc->Ialpha =  lpFoc->Ia;
	lpFoc->Ibeta = ( lpFoc->Ia + ( 2 * lpFoc->Ib ) ) * divSQRT3;
}

void mcPark(LP_MC_FOC lpFoc)
{
	lpFoc->Id = +lpFoc->Ialpha * lpFoc->fCosAngle + lpFoc->Ibeta * lpFoc->fSinAngle;
	lpFoc->Iq = -lpFoc->Ialpha * lpFoc->fSinAngle + lpFoc->Ibeta * lpFoc->fCosAngle;
}

void mcInvPark(LP_MC_FOC lpFoc)
{
	lpFoc->Valpha = lpFoc->Vd * lpFoc->fCosAngle - lpFoc->Vq * lpFoc->fSinAngle;
	lpFoc->Vbeta  = lpFoc->Vd * lpFoc->fSinAngle + lpFoc->Vq * lpFoc->fCosAngle;
}

void mcInvClark(LP_MC_FOC lpFoc)
{
	lpFoc->Vb = lpFoc->Vbeta;
	lpFoc->Va = ( -lpFoc->Vbeta + ( SQRT3 * lpFoc->Valpha ) ) * 0.5f;
	lpFoc->Vc = ( -lpFoc->Vbeta - ( SQRT3 * lpFoc->Valpha ) ) * 0.5f;
}

void mcPMSM_QD_PID(LP_MC_FOC lpFoc)
{
	if( lpFoc->enable ) {
		if( lpFoc->Iq_des >  1900.0f ) lpFoc->Iq_des =  1575.0f;
		if( lpFoc->Iq_des < -1900.0f ) lpFoc->Iq_des = -1575.0f;

		//FirstOrderLagFilter( &lpFoc->Id_des_filter, lpFoc->Id_des, 0.99 );
		lpFoc->Id_des_filter = lpFoc->Id_des;

		FirstOrderLagFilter( &lpFoc->Iq_des_filter, lpFoc->Iq_des, 0.99 );
		//lpFoc->Iq_des_filter = lpFoc->Iq_des;

		lpFoc->Vd = pidTask( &lpFoc->pid_d, lpFoc->Id_des_filter, lpFoc->Id );
		lpFoc->Vq = pidTask( &lpFoc->pid_q, lpFoc->Iq_des_filter, lpFoc->Iq );
	} else {
		lpFoc->pid_d.sumError = 0.0f;
		lpFoc->pid_q.sumError = 0.0f;

		lpFoc->Id_des_filter = 0;
		lpFoc->Iq_des_filter = 0;

		lpFoc->Id_des = 0.0f;
		lpFoc->Iq_des = 0.0f;

		lpFoc->Vd = 0.0f;
		lpFoc->Vq = 0.0f;
	}
}

void mcUsrefLimit(LP_MC_FOC lpFoc)
{
	float limit = lpFoc->m;
	float Usref, scale;

	Usref = sqrtf( lpFoc->Vd * lpFoc->Vd + lpFoc->Vq * lpFoc->Vq );

	if( Usref > limit ) {
		scale = limit / Usref;
		lpFoc->Vd *= scale;
		lpFoc->Vq *= scale;
	}
}

void ADC_IRQHandler( void )
{
	static int32_t counter_pos_reg = 0, counter_speed_reg = 0;
	static int32_t counter_get_speed = 0;
	static float arrSpeedFB[10] = { 0 };
	static uint16_t angle = 0;

	GPIO_SetBits( GPIOB, GPIO_Pin_2 );

	if( ADC_FLAG_JEOC & ADC1->SR ) {
#ifdef FOC_ADC_Mode_Independent
		lpFoc->current_a = ADC_GetInjectedConversionValue( ADC1, ADC_InjectedChannel_1 );
		lpFoc->current_b = ADC_GetInjectedConversionValue( ADC1, ADC_InjectedChannel_2 );
#endif

#ifdef FOC_ADC_DualMode_RegSimult_InjecSimult
		lpFoc->current_a = ADC_GetInjectedConversionValue( ADC1, ADC_InjectedChannel_1 );
		lpFoc->Ubus = ADC_GetInjectedConversionValue( ADC1, ADC_InjectedChannel_2 );
#endif
	}

	if( ADC_FLAG_JEOC & ADC2->SR ) {
#ifdef FOC_ADC_Mode_Independent
		dc_voltage = ADC_GetInjectedConversionValue( ADC2, ADC_InjectedChannel_1 );
		ai0 = ADC_GetInjectedConversionValue( ADC2, ADC_InjectedChannel_2 );

		if( !(ADC_FLAG_JEOC & ADC1->SR) ) {
			ADC_ClearITPendingBit( ADC2, ADC_IT_JEOC );
			return;
		}
#endif
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

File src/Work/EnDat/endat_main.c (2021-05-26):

/*
 * Project: STMBL - https://github.com/rene-dev/stmbl
 * File: https://github.com/rene-dev/stmbl/blob/master/src/comps/endat.c
 *
 * endat.c
 *
 *  Created on: Nov 23, 2020
 */

#include "endat.h"

#define MIN(a,b) (((a)<(b))?(a):(b))
#define MAX(a,b) (((a)>(b))?(a):(b))

const uint64_t bitmask[] = {
  0b0,
  0b1,
  0b11,
  0b111,
  0b1111,
  0b11111,
  0b111111,
  0b1111111,
  0b11111111,
  0b111111111,
  0b1111111111,
  0b11111111111,
  0b111111111111,
  0b1111111111111,
  0b11111111111111,
  0b111111111111111,
  0b1111111111111111,
  0b11111111111111111,
  0b111111111111111111,
  0b1111111111111111111,
  0b11111111111111111111,
  0b111111111111111111111,
  0b1111111111111111111111,
  0b11111111111111111111111,
  0b111111111111111111111111,
  0b1111111111111111111111111,
  0b11111111111111111111111111,
  0b111111111111111111111111111,
  0b1111111111111111111111111111,
  0b11111111111111111111111111111,
  0b111111111111111111111111111111,
  0b1111111111111111111111111111111,
  0b11111111111111111111111111111111,
  0b111111111111111111111111111111111,
  0b1111111111111111111111111111111111,
  0b11111111111111111111111111111111111,
  0b111111111111111111111111111111111111,
  0b1111111111111111111111111111111111111,
  0b11111111111111111111111111111111111111,
  0b111111111111111111111111111111111111111,
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
};

union
{
  uint64_t data;
  uint8_t dataa[8];
} df, df1, df2, df_pos;

endat_data_t en_data_value;
endat_data_t data;
endat_cmd_t req;
//////////////////////////////
extern SPI_HandleTypeDef hspi3;
//////////////////////////////
uint64_t shift = 0;

uint8_t error = 0;
uint8_t state = 0;

uint8_t pos_len = 17;
uint8_t mpos_len = 0;
uint8_t endat_state = 13;
uint8_t swap = 0;
uint8_t skip = 10;
uint8_t bytes = 7;

void en_dat_inti(void)
{
}

uint32_t endat_tx(endat_cmd_t cmd, uint8_t p1, uint16_t p2, uint8_t* buf, endat_data_t* data){
  uint32_t len = 0;

  buf[0] = flip8(cmd);

  buf[1] = flip8(p1);

  buf[2] = flip16(p2) & 0xff;
  buf[3] = (flip16(p2) >> 8) & 0xff;

  data->current_cmd = cmd;
  data->current_addr = p1;
  data->current_value = p2;

  switch(cmd){
    case ENDAT_READ_POS:
      len = 2 + 6;
    break;

    case ENDAT_SELECT_MEM:
      len = 2 + 6 + 8 + 16;
      data->current_mem = p1;
    break;

    case ENDAT_READ_ADDR:
      len = 2 + 6 + 8 + 16;
    break;

    case ENDAT_WRITE_ADDR:

      len = 2 + 6 + 8 + 16;
    break;

    case ENDAT_RESET:
      len = 2 + 6 + 8 + 16;
    break;

    default:
      len = 0;
  }

  return(len);
}

uint32_t endat_rx(uint8_t* buf, uint32_t max_len, endat_data_t* data)
{
  union{
    uint64_t data64;
    uint32_t data32[2];
    uint16_t data16[4];
    uint8_t data8[8];
  }df;

  uint32_t len = 0;

  endat_cmd_t cmd = data->current_cmd;
  data->current_cmd = 0;

  uint8_t addr = data->current_addr;
  data->current_addr = 0;

  uint16_t value = data->current_value;
  data->current_value = 0;

  switch(cmd){
    case ENDAT_READ_POS:
      len = 1 + 1 + data->pos_bits + data->mpos_bits + 5;
    break;

    case ENDAT_SELECT_MEM:
      len = 1 + 8 + 16 + 5;
    break;

    case ENDAT_READ_ADDR:
      len = 1 + 8 + 16 + 5;
    break;

    case ENDAT_WRITE_ADDR:
      len = 1 + 8 + 16 + 5;
    break;

    case ENDAT_RESET:
      len = 1 + 8 + 16 + 5;
    break;

    default:
      return(0);
  }

  if(max_len < len){ // too short
    return(0);
  }

  for(int i = 0; i < (len + 7) / 8; i++){ // local copy
    df.data8[i] = buf[i];
  }

  uint8_t error_bit = 0;
  uint64_t temp1 = 0;
  uint64_t temp2 = 0;
  uint8_t p1;
  uint16_t p2;

  switch(cmd){
    case ENDAT_READ_POS:
      error_bit = df.data8[0] & 0x10;

      df.data64 >>= 2; // remove start + error bit
      temp1 = df.data64 & bitmask[data->pos_bits];
      df.data64 >>= data->pos_bits; // remove pos
      temp2 = df.data64 & bitmask[data->mpos_bits];
      df.data64 >>= data->mpos_bits; // remove mutliturn pos
      data->crc = df.data64 & bitmask[5];

      //check crc
      data->error_bit = 0;
      if(error_bit){
        data->error_bit = 1;
        //return(0);
      }
      data->pos = temp1;
      data->mpos = temp2;
    break;

    case ENDAT_SELECT_MEM:
      p1 = (df.data16[0] >> 1) & 0xff;
      data->crc = (df.data8[3] >> 1) & 0b11111;
      p1 = flip8(p1);

      //check crc
      if(data->current_mem != p1){
        data->current_mem = 0;
        return(0);
      }
    break;

    case ENDAT_READ_ADDR:
      p1 = (df.data16[0] >> 1) & 0xff;
      p2 = (df.data32[0] >> (1 + 8)) & 0xffff;
      data->crc = (df.data8[3] >> 1) & 0b11111;
      p1 = flip8(p1);
      p2 = flip16(p2);

      //check crc
      if(addr != p1){
        return(0);
      }

      switch(data->current_mem){
        case ENDAT_MEM_STATE:
          switch(p1){
            case 0: // error register
              // data->error = *((endat_state_error_t*) &p2);
              data->error.reg = p2;
            break;

            case 1: // warning register
              // data->warning = *((endat_state_warning_t*) &p2);
              data->warning.reg = p2;
            break;

            default:
              return(0);
          }
        break;

        case ENDAT_MEM_PARAM0:
          switch(p1){
            case ENDAT_ADDR_POS_LEN:
              data->pos_len = p2;
              data->pos_bits = data->pos_len - data->mpos_bits;
            break;

            case ENDAT_ADDR_TYPE:
              data->fb_type = p2;
            break;

            default:
              return(0);
          }
        break;

        case ENDAT_MEM_PARAM1:
          switch(p1){
            case ENDAT_ADDR_MULTITURN:
              data->mpos_bits = log2f(p2) + 0.99;
              data->pos_bits = data->pos_len - data->mpos_bits;
            break;

            case ENDAT_ADDR_RES_LOW:
              data->pos_res = (data->pos_res & 0xffff0000) | p2;
            break;

            case ENDAT_ADDR_RES_HIGH:
              data->pos_res = (data->pos_res & 0xffff) | (p2 << 16);
            break;

            default:
              return(0);
          }
        break;

        case ENDAT_MEM_PARAM2:
          switch(p1){
            case ENDAT_ADDR_MAX_VEL:
              data->max_vel = p2;
            break;

            default:
              return(0);
          }
        break;

        default:
          return(0);
      }

    break;

    case ENDAT_WRITE_ADDR:
      p1 = (df.data16[0] >> 1) & 0xff;
      p2 = (df.data32[0] >> (1 + 8)) & 0xffff;
      data->crc = (df.data8[3] >> 1) & 0b11111;
      p1 = flip8(p1);
      p2 = flip16(p2);

      //check crc
      if(addr != p1){
        return(0);
      }
      if(value != p2){
        return(0);
      }
    break;

    case ENDAT_RESET:
      data->crc = (df.data8[3] >> 1) & 0b11111;
      //check crc
    break;
  }

  return(1);
}

volatile uint64_t post = 0;
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

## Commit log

2017-05-21 update
    And now in FOC mode :)
    [main.brd, main.sch]
2017-12-23 Edit Power Stage
    [main.brd, main.sch]
2017-12-23 Prevent saturation of Vsref (input for SVPWM)
    [foc.c, foc.cpp, main.cpp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]
2017-12-24 Test position and speed PID's
2019-04-20 Fix AM26LS31 to AM26LS32ACD in schematic
    [RES-SIN-COS.SDF, main.brd, main.sch]
2019-04-26 HCPL-7xx
    Add HCPL-7xx.sch && HCPL-7xx.brd to schematic folder
    [HCPL-7xx.brd, HCPL-7xx.sch]
2019-12-22 Edit ADC Init
2020-10-30 Add "VoltageSensing"
    [main.brd, main.sch]
2022-06-11 Update endat.c with current test file
2023-01-28 Rebuild with GNU Arm Embedded Toolchain 10 2021.10
2024-03-01 XML-SE30AЕКЕ Images
    1) Add XML-SE30AЕКЕ images
    2) Update Rectifier
2024-03-01 Add XML-SE30AЕКЕ Images

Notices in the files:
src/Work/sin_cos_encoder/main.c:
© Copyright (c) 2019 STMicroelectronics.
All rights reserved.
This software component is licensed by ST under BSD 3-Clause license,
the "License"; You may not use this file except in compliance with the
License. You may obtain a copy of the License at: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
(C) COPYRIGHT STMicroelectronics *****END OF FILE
